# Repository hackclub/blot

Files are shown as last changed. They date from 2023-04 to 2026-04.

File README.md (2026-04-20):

# Blot, the plotter bot from Hack Club

**[🕸 Landing Page](https://blot.hackclub.com)** | **[💻 Online Editor](https://blot.hackclub.com/editor)** | **[👀 Gallery](https://blot.hackclub.com/gallery)**

> Saw Blot at [RMRRF](https://rmrrf.com) 2026? That was a fork of the firmware, check it out [here](https://github.com/samdev-7/upgraded-blot).

Create programmatic art in our web-based editor and submit it to the gallery and we'll send you a CNC machine which can make that art for free.
Blot is a [**You Ship, We Ship**](https://github.com/hackclub/blot/tree/main?tab=readme-ov-file#you-ship-we-ship) project from [Hack Club](https://hackclub.com).

> Everything about Blot is open source. The online editor and drawing library can be freely used by anyone, and we encourage all to submit to the gallery through PRs! However, you must be a teenager or younger to receive a free machine.

blot-white-bg

A piece of art made for Blot can be the first program you ever write, but it can also be a challenge for a master programmer. Check out some of the art made already in our [gallery](https://blot.hackclub.com/gallery). Every piece of art you see is actually a program. Many of them create unique pieces every time the art is run. You may be looking at an artwork which has never been seen before, even by the creator.

For a short video introduction to Blot [check out our 38 second trailer](https://www.youtube.com/watch?v=d1noJNmfvC0).

<a href="https://www.youtube.com/watch?v=d1noJNmfvC0">
  
</a>

# How It Works

### 1) Create a piece of programmatic art in the web editor.

To learn the Blot drawing library follow our [getting started guide](https://blot.hackclub.com/editor?guide=start). Check out the examples in the [gallery](https://blot.hackclub.com/gallery) and then follow along with some of our [guides](https://blot.hackclub.com/guides).

editor

### 2) Submit that art to the public gallery.

The [submission rules to get a Blot for a PR are here](https://github.com/hackclub/blot/blob/main/docs/GET_A_BLOT.md). **You must be a teenager (or younger to qualify for a free machine)** but anyone can make art and make a PR.

[](https://blot.hackclub.com/gallery)

### 3) Receive the parts to build your own Blot that can draw that art in real life.

The [bill of materials can be found here](/docs/BOM.toml) and an [assembly guide here](https://blot.hackclub.com/assembly).

all-parts



<!-- <img height="341" alt="drawing" src="https://github.com/hackclub/blot/assets/27078897/2f7c9c17-3b67-4674-b2ca-2a4dbd26a3d1" /> -->

# Blot is...

**A custom CNC drawing machine** designed from scratch to introduce you to digital fabrication.
It's made of 6 unique 3D printed parts with a custom control board and easy to understand firmware, which can be interfaced with through JavaScript in the browser.
Blot is designed in OnShape. Check out the [3D model of the project](https://cad.onshape.com/documents/536478c2ac00624edd8e2182/w/945ceabd15096661108b7650/e/61fd4346c9fdab983c6ba24d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).
You can find the [bill of materials here](https://blot.hackclub.com/assembly) and, if you'd like to 3D print your Blot, [the parts are here](https://github.com/hackclub/blot/tree/main/hardware/mechanical/drawing-thing-v4). The entire build costs about $150 dollars. If you're a teen we will give you all the parts for a PR with your an art piece you coded yourself.

**A web based editor for programmatic art** that we designed specifically for pen plotting with a [custom geometry library](/docs/DOCUMENTATION.md).
We practiced programmatic pen plotting with [some](https://github.com/LingDong-) [amazing artists](https://static1.squarespace.com/static/63fbc39db5b01b5fa30423db/t/649b424d33b2ce3e0d5b63a5/1687896656015/June+Cohort+Zine.pdf).
There is so much to learn and explore on the programming and the aesthetic side.

parts



# Blot Docs

Here are a collection of resources for Blot:

- [Complete documentation of the drawing library in the editor](https://github.com/hackclub/blot/blob/main/docs/DOCUMENTATION.md)
- [Short documentation shown in the Blot editor](https://github.com/hackclub/blot/blob/main/public/TOOLKIT.md)
- [The Blot assembly and operation guide](https://github.com/hackclub/blot/blob/main/docs/assembly/ASSEMBLY.md)
- [The source of truth bill of materials (BOM)](https://github.com/hackclub/blot/blob/main/docs/BOM.toml)
- [Criteria for how to get a Blot and a guide on how to submit a PR](https://github.com/hackclub/blot/blob/main/docs/GET_A_BLOT.md)
- [A guide on how to review Blot submissions](https://github.com/hackclub/blot/blob/main/docs/BLOT_REVIEW.md)
- [A brief guide on how to approve Blot requests for Blot shipments](https://github.com/hackclub/blot/blob/main/docs/APPROVING_BLOT_REQUESTS.md)
- [Information on how we order Blot supplies from our manufacturing partners](https://github.com/hackclub/blot/blob/main/docs/ORDERING_BLOT_KITS.md)
- [The files for the 3D printed parts](https://github.com/hackclub/blot/tree/main/hardware/mechanical/blot-v6)
- [The source files for the control PCB](https://github.com/hackclub/blot/tree/main/hardware/motor-control-board/circuit/controller)
- [The source files for the power delivery PCB](https://github.com/hackclub/blot/tree/main/hardware/motor-control-board/circuit/power-delivery)
- [The firmware for the Blot control board](https://github.com/hackclub/blot/blob/main/hardware/motor-control-board/firmware/firmware.ino)
- [Sample Blot based lesson plan](https://github.com/hackclub/blot/blob/main/docs/lesson/LESSON-PLAN.md)
- [Video of a Blot being assembled](https://www.youtube.com/watch?v=7N-Nu6_oo4I)
- [Video of operating a Blot](https://www.youtube.com/watch?v=qDP5CNjFHJE)
- [Video of making a Blot submission](https://www.youtube.com/watch?v=AmbjNEPuv14)
- [Video Blot promo trailer](https://www.youtube.com/watch?v=d1noJNmfvC0)
- [Video introduction to JavaScript in the context of Blot](https://www.youtube.com/watch?v=3KAan1PzmxA)
- [Video introduction to Blot editor](https://www.youtube.com/watch?v=OZ9KaFr1V_o)
- [Video demonstrating working through a Blot guide](https://www.youtube.com/watch?v=mP4rUdaF8ng)

# What are People Making with Blot

Blot has been in development since January 2023 and was released April 2024. We've had lots of people use the Blot editor and the Blot machine to create visual art, run workshops and as part of interactive installations. Here's a sense of what can be done with Blot.

### Programmatic Art

There are all sorts of styles of programmatic art. Here are some examples of great Blot submissions that show a range of styles. This list is by no means exhaustive.

**The natural scene** is a common source of artistic inspiration. This could be called figurative or representational art when it tries to depict a real thing with some fidelity. One example are these roots by Kai (age 17).

<a href="https://blot.hackclub.com/editor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">
  collection
</a>

**The geometric pattern** is natural avenue to pursue when making art with computers because code is a great way to describe patterns. Oz's approach of clipping overlapping segments creates a wonderful sense of depth.

<a href="https://blot.hackclub.com/editor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">
  
</a>

**The tech demo (with composition)** is focusing on a specific technical approach like in Henry's (age 15) ray marcher. The art piece isn't complete though until the artists uses the technique to make a composition.

<a href="https://blot.hackclub.com/editor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">
  <picture>
    <source media="(prefers-color-scheme: dark)" srcset="https://github.com/hackclub/blot/assets/61765149/d65464eb-8cc2-4bf3-be82-0b4cc12070bd">
    <source media="(prefers-color-scheme: light)" srcset="https://github.com/hackclub/blot/assets/27078897/90c01a52-0404-423f-8ae9-763bc591ff9f">
    
  </picture>
</a>

**The data transformation** can be seen in Kieran's (age 15) self portrait. It takes data from an SVG but modifies it programmatically to produce an art piece. This approach could be used to visualize data that may not of been visual to begin with.

<a href="https://blot.hackclub.com/editor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">
  
</a>

**The concept** is important with any artwork and can be mixed with any of the genres above. Ultimately an interesting idea can be what elevates something that is visually pretty simple, one example by Ayush is the Blot's own self portrait.

<a href="https://blot.hackclub.com/editor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">
  <picture>
    <source media="(prefers-color-scheme: dark)" srcset="https://github.com/hackclub/blot/assets/61765149/12044cdf-a498-438c-814b-48622488e42f">
    <source media="(prefers-color-scheme: light)" srcset="https://github.com/hackclub/blot/assets/27078897/1f367d9b-aa74-4fca-8623-259a06800335">
    
  </picture>
</a>

For way more examples check out the [gallery](https://blot.hackclub.com/gallery).

### Blot as Creative Material

You ship we ship projects are developed to provide technological creative material. The Blot was developed to not just create visual programs on computers but also to explore robotic and interactive technology. Here are some ways the machine or project has been used to create interactive technology experiences.

[**Lineflow**](https://github.com/leomcelroy/lineflow) was developed as an interactive art piece for an MIT Museum event. Participants would create a single line drawing on the computer and would then watch a simulation of a line folding into their drawing. Three frames of that simulation were strung together to create a timeline of the animation that would be drawn by a Blot to be brought home by the participant.





**The infinite gallery** at [Outernet](https://www.youtube.com/watch?v=O1s5HqSqKi0) (Hack Club's 2023 summer hackathon). Leo, Kai, and Henry constructed a black out box that contained an infinite art gallery. Participant's entered a room sized black box with one wall illuminated with artwork and a giant joystick in the center. They could navigate the gallery with the joystick and as they explored new (possibly never before seen) art was generated based on their location.



**Chinese calligraphy workshop** was developed for and run at the [Hack Club leader summit 2024](https://www.youtube.com/watch?v=UZEm5lONg7g) by Bright Li (age 15). During it participants learned how to draw Chinese calligraphy programmatically and then handed ink brushes to Bright's Blot robot to put the drawings to the page.



# It's All Open Source

Every part of Blot is freely available for you to investigate and discover.
That includes the editor, the hardware design, the electronics, and even the finances around the project.
We think people deserve tools they can take ownership of. That's why we give away the source for free.

Our projects at Hack Club have hundreds of teenage contributors from all over the world. If you want to learn how to program, we invite you to jump in and start building tools used by thousands.

You're also welcome to participate and use our tools if you aren't a teen (like making art or building your own blot), but our [online community](https://hackclub.com/slack) is for teens only.

# You Ship, We Ship

At Hack Club we're reimagining a new type of public education for technology. We believe people learn best by creating things they care about and sharing them with others. We build open source creative tools with young people all around the world. These tools are gateways to new subjects in technology like [embedded systems](https://sprig.hackclub.com), [circuits](https://onboard.hackclub.com) or digital fabrication robotics. When teenagers build things with our tools we send them more creative materials for free.

Our goal is to build a new type of library online that offers learners not just media to consume but tools to create. And it is free and open source to all. We're just getting started...

# Development

Join the `#blot` channel on the [Hack Club Slack](https://hackclub.com/slack).

The Blot editor is run with an Express server.

After installing `Git`, `Node.js`, and `Yarn`, clone the repo.

```
git clone https://github.com/hackclub/blot/
yarn install
```

To run the development server:

```
yarn dev
```

# License

The Hack Club Blot is open source and licensed under the [MIT License](https://github.com/hackclub/blot/LICENSE.md). Fork, remix, and make it your own! Pull requests and other contributions greatly appreciated.

# Acknowledgements

Many people have contributed to Blot, to mention a few and give much thanks too...

MIT's Center for Bits and Atoms for providing expert advice and occasionally a space to work.

Sam Hu and his team at ISourceAsia for supplying Blot parts and becoming a critical part of the Blot team.

Paul Hamilton for his contributions to embedded circuit designs.

Oz Nova for writing an excellent getting started guide.

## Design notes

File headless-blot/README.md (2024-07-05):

# TeleBlot

Blot is a plotter bot from Hack Club. The TeleBlot Site encourages Hack Clubbers to create with Blot by lowering the barrier for Hack Clubbers to see their Blot works drawn on a Blot machine. Hack Clubbers can upload code to the website and watch through a livestream as a remote blot machine (the TeleBlot) draws their code.

image (2)

image (1)

## Components
- Raspberry Pi Model B (RPi)
- LCD Writing Tablet (modified)
- USB Webcam (generic)
- Blot from Hack Club

## Setup
The setup requires:
- [ ] RPi connected to WiFi
- [ ] *USB Webcam* and *Blot* connected to RPi through USB
- [ ] *LCD Writing Tablet* connected to RPi through GPIO (connect the tablet's ground wire to the RPi's ground GPIO pin and the tablet's postive wire to the RPi's BOARD_PIN GPIO, default: 7)
- [ ] Position the *USB Webcam* to look at the *LCD Writing Tablet*

On the RPi in the `headless-blot` directory run:
1. `yarn install`
2. `sudo apt-get install motion`
3. `sudo chown motion:motion /etc/motion`
4. `sudo cp motion.conf /etc/motion/motion.conf`

## Running
1. Start the Motion daemon: `sudo systemctl start motion`
2. Start the server: `yarn run`
3. To test, upload a blot code file (.js) to the "Teleblot" Slack Bot on the Hack Club Slack, you should receive 1) a video of the Blot drawing your sketch and 2) an image of the result.

### Note
- Any changes to motion.conf must be copied to: `sudo cp motion.conf /etc/motion/motion.conf` and the Motion daemon restarted: `sudo systemctl start motion`
- Once started, the Motion daemon will run automatically in the background, even after restarting the RPi
- The USB webcam livestream can be found at http://<rpi_ip>:8081 and exposed externally with a reverse proxy such as [LocalXpose](https://localxpose.io/)

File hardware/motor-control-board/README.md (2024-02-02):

# Blot Control Board

The assembled blot control board is a main board with a set of smaller boards attached to it's headers:

- 1x Blot Control Board ([designed in house](./circuit/controller/))
    - 2x A4988 stepper motor drivers
    - 1x Seeeduino XIAO RP2040
    - 1x USB-C Power Delivery board ([designed in house](./circuit/power-delivery/))
    - 1x Stepper motor breakout board ([designed in house](./circuit/stepper-motor-headers/))

A set of three assembled control boards and decoy boards

The KiCAD project files are provided in the repo and are designed with KiCAD v7. This may not be compatible with previous versions, but you can get the latest version [here](https://www.kicad.org/download/). 

## Carrier Board

The carrier board wires the breakouts together, provides external power circuitry for the A4988 and steppers, and a convenient way to mount the board to the blot machine. It's a simple 2-layer 1.6mm PCB measured at 50x70mm. It also has a pin header breaking out 5 unused GPIO pins, including 1 DAC channel, 2 analog-capable pins, and one I2C bus. 

KiCAD Render of Carrier Board

## Power Delivery Board

The power delivery board provides a fixed output of 9V1A using the CYPD3177 chipset. It's highly flexible, allowing USB-C Charging up to 15W and USB-C PD up to 100W. Unlike many other chips available, it does not require any firmware nor flashing, and power settings are configured with pullup and pulldown resistors. This board is set to 9V @ 1A, to ensure maximum compatibility with most PD-capable bricks. It's very compact, measuring less than 22x32mm with breadboard-friendly mounting, an affordable 2-layer design, and single side SMD component placement. 

During prototyping, we used an off-the-shelf module from Amazon. These only had four 2.54mm pins on the edge of the board and were hard to mount onto the board securely. Building our own also gave us better control over supply of these boards. 

*As a precaution: while this board is breadboard friendly, typical solderless breadboards are only rated up to _5V @ 1A_. Do _not_ use this on a solderless breadboard.*

KiCAD Render of PD Board

## Additional Relevant Reading

Below is a list of datasheets / product briefs that may be relevant. 

[Seeeduino RP2040 XIAO](https://wiki.seeedstudio.com/XIAO-RP2040/)\
[A4988 Breakout Board](https://www.pololu.com/product/1182)\
[CYPD3177](https://www.infineon.com/cms/en/product/universal-serial-bus/usb-c-charging-port-controllers/ez-pd-barrel-connector-replacement-bcr/cypd3177-24lqxq/)\
[DMP3013SFV](https://www.diodes.com/assets/Datasheets/DMP3013SFV.pdf)\
[MM3Z15VC](https://www.onsemi.com/pdf/datasheet/mm3z9v1c-d.pdf)\
[WCAP-ATG5](https://www.we-online.com/components/products/datasheet/860020573008.pdf)\
[JS Series Switch](https://www.ckswitches.com/media/1422/js.pdf)\
[Schottky Diode](https://datasheets.kyocera-avx.com/schottky.pdf)

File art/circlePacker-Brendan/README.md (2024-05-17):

Circle Packer fills the page with circles suboptimally.

Most of the code was reused and adapted from a [project I did a year ago](https://github.com/Brelee2222/CLUCK/blob/main/src/frontend/dash/circlePacker.ts)

The packer works by attempting to fit circles in between two others. If the circle cannot be fit, the size is reduced is attempts to fit the circle again.

These are the following configurable values that will change how the blot will print:<br />
* targetAreaFill -- This value changes how much the circles need to fill of the area before the program stops generating circles.
* minCircleSize -- This value sets a minimum radius a circle needs to be in order to be shown/printed by the blot.
* bt.setRandSeed(seed); -- Sets a seed to the randomness.

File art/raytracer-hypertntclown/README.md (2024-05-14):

# Raytracer

This is a raytracer, currently able to render spheres and triangles, I built based on concepts learned from [Computer Graphics from Scratch](https://gabrielgambetta.com/computer-graphics-from-scratch/). I highly recommend anyone who's interested in building their own raytracer to check this out.

It has two "modes". Mainly there is the one adapted to use a post processing filter to render it as grayscale ascii-art with a limited character-set as otherwise it would for sure not have been able to be drawn by a Blot.
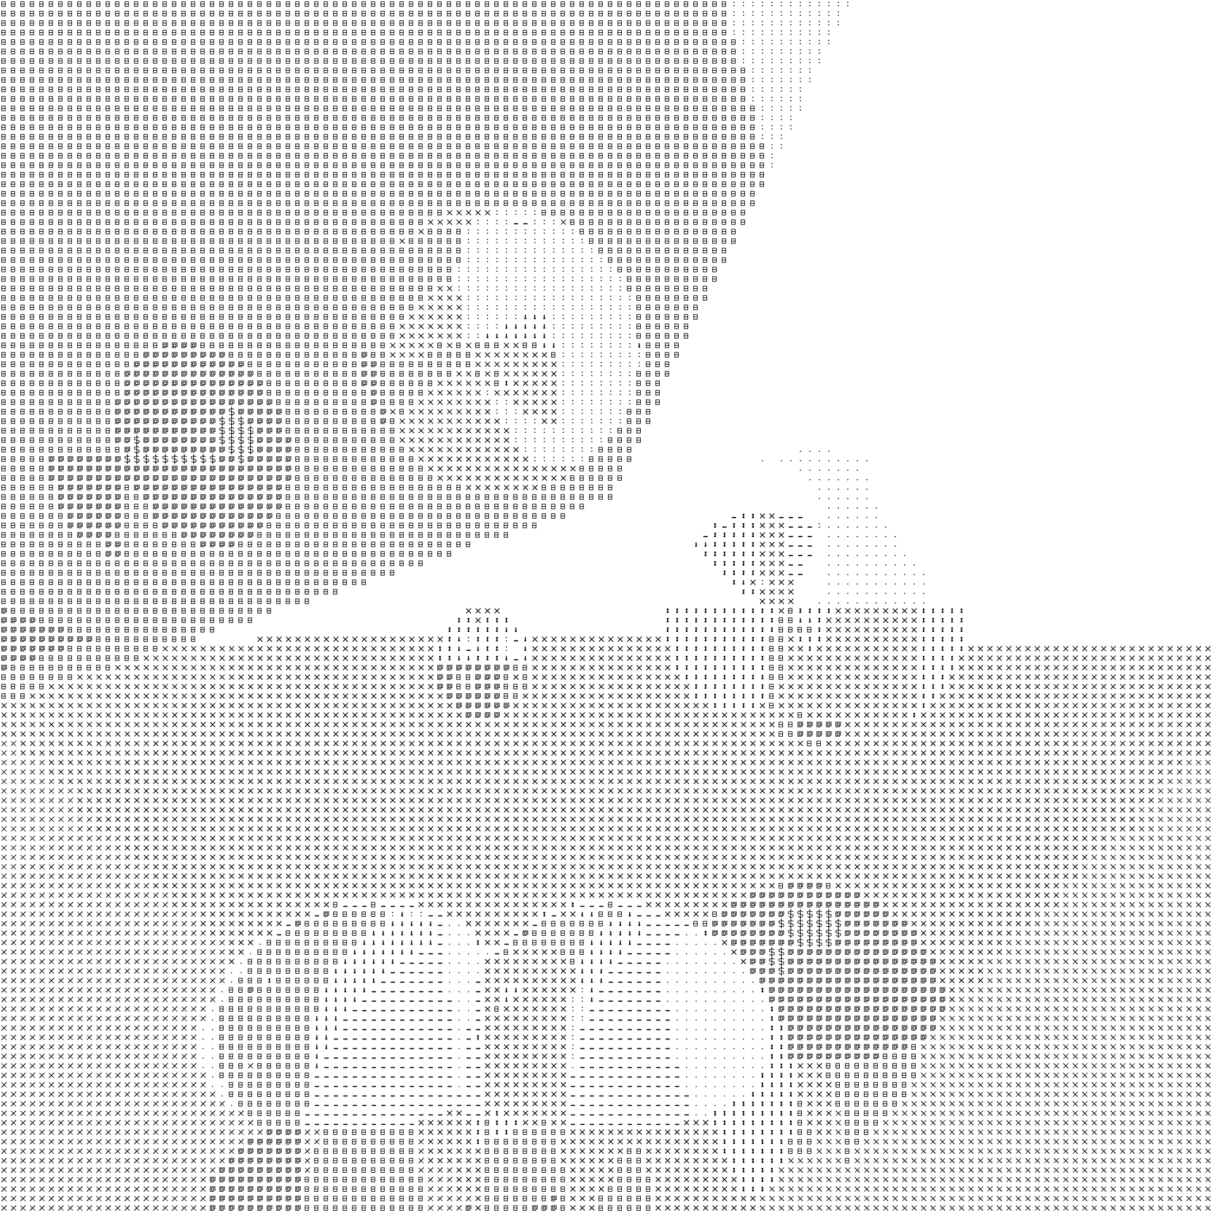
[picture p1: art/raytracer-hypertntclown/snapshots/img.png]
SinArt


The second "mode", activated by changing a boolean at the top of the script, shows the raytraced result before being filtered.
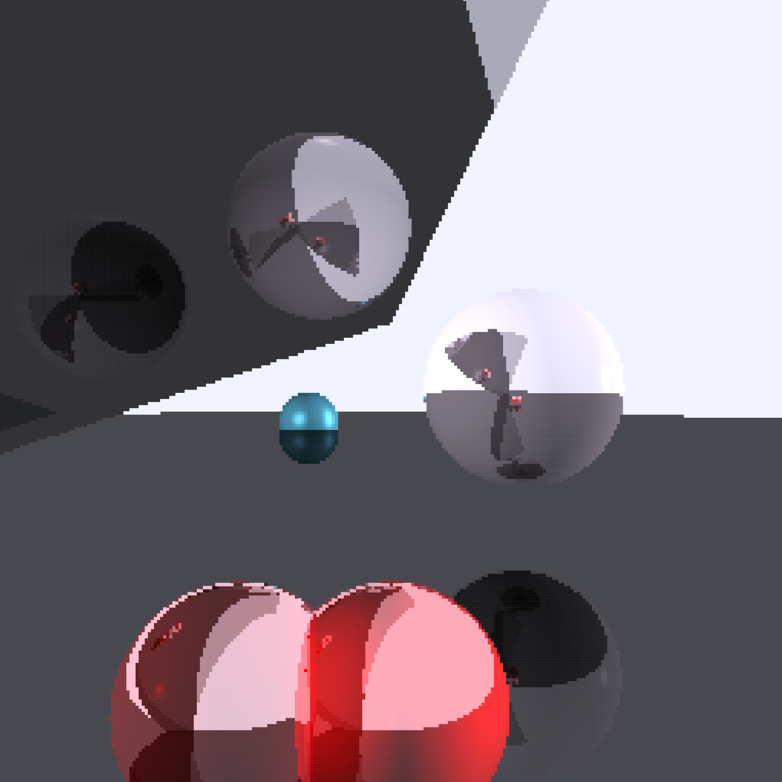
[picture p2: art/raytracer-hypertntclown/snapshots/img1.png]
Raytrace


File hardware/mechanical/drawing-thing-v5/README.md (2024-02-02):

- CarriagePlate.stl is assembled from aluminum plate
- For the carriage, you can either print EccentricCarriage.stl by itself, or print ReinforcedCarriage.stl and add the aluminum CarriagePlate.stl to it during assembly

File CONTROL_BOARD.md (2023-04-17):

# WIP

# [A single control board](https://leomcelroy.com/svg-pcb/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)

Ultimately the idea is that each device will have it's own little board which we network together through modular things. 
For development purposes (and for the sake of doing due diligence) I decided to make a single control board as well which the two steppers and single servo and plug into.
It saves money because the board only requires one xiao instead of three.

I decided to use SVG PCB to design the board because I'm pretty comfortable with the software (because I wrote it).
Additionally, a community contributor to the project (Kris) recently added Gerber export which I was eager to use.

https://tracespace.io/view/
https://www.amazon.com/gp/product/B08NFKV2LD/ref=ppx_yo_dt_b_asin_title_o00_s00?ie=UTF8&psc=1
https://jsoneditoronline.org/#left=local.linisi
https://www.snapeda.com/parts/102010388/Seeed%20Technology%20Co.%2C%20Ltd/view-part/?ref=search&t=xiao

Seeeduino-XIAO-pinout-1
0J10073 600



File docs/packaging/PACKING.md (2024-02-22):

Hey there! If you're reading this, you're probably trying to pack a blot to ship out to a hack clubber.

You'll probably want to familiarize yourself with the [BOM](../BOM.toml) before packing.

Here's a quick checklist of what to include:

- [ ] Welcome to blot letter
- [ ] Box 1: screws
- [ ] Box 2: belt and flanged bearings
- [ ] Box 3: v-wheel box
- [ ] Box 4: nuts
- [ ] Box 5: electronics
- [ ] Tool bundle
- [ ] Floating parts

Each box should be pre-assembled before packing a blot box & each of the parts should be QA tested before going into their respective boxes. Each box has a checklist of parts, and a following section on how to test the parts. Not all parts need to be tested.

## Welcome to blot letter

This is a letter that accompanies every blot. It's a quick, friendly message and includes a screw size guide. It's drawn on small cardstock using a blot.



The code for drawing this on a blot can be found in [notecard.js](./notecard.js). Please make sure to increment the blot number on the card before shipping & documenting on Airtable's list of Blot orders when you send a Blot with a specific number.

## Box 1: screws

- [ ] A paper bag containing:
  - [ ] M3x10 screws (x9) (1 more than required)
  - [ ] metal shims (x6) (1 more than required)
- [ ] M5x20, cyl. head (x1)
- [ ] M5x20 (x6) (1 more than required)
- [ ] M5x35 (x11) (1 more than required)
- [ ] M5x10 (x14) (1 more than required)

**Testing**

A screw size guide is included in the welcome to blot letter. Each group of screws should be tested before being packed.

## Box 2: belt and flanged bearings

- [ ] timing belt
- [ ] 1 flanged bearing tube (which contains at least 10 flanged bearings)

**Testing**

To test the timing belt, hold it up to the master belt and ensure it's at least as long and no longer than 1 inch longer than the master belt.

To test the flanged bearings inside the tube, make sure they take up most of the tube to ensure we don't pack a tube with too few bearings.

## Box 3: v-wheel box

This box should contain:
- [ ] 12 V-wheels (1 more than required).

**Testing**

V-wheels should be tested by inserting a M5 screw of any length to ensure they spin freely.

## Box 4: nuts

This box should contain:
- [ ] M5 T-nut (x14) (1 more than required)
- [ ] M5 nut (x18) (1 more than required)
- [ ] Timing belt pulley (x2)
- [ ] Metal Spacer (x4)
- [ ] Eccentric Spacer (x5)
- [ ] 4 rubber feet stickers

**Testing**

To test the timing belt pulley, quickly screw it into a stepper motor and try turning the motor to ensure it has a firm grip on the stepper motor axle.

## Box 5: Electronics

The electronics box should contain:
- [ ] usb-c power cable + brick
- [ ] usb-c male-male data cable
- [ ] 2 stepper motor 6-pin to 4-pin cables
- [ ] anti-static bag containing:
  - [ ] [blot main board](../../hardware/motor-control-board), assembled & packed in an anti-static bag
    - [ ] 2 stepper driver
    - [ ] 1 xiao seeed rp2040
    - [ ] usb-c power distribution board
    - [ ] [horizontal stepper breakout](https://cloud-9z8rqqzj6-hack-club-bot.vercel.app/0img_0759.jpg)
  - [ ] servo motor
  - [ ] servo motor arm

**Testing**

To test the electonics, plug the steppers and servo into the main board, and try to run any of the art examples in the gallery.[^0][^1]

[^0]: Your xiao rp2040 will flash 3 times on it's red LED if flashed.
[^1]: If your xiao rp2040 isn't flashed, or acting strangly, use the flashing instructions provided in [the hardware instructions](../../hardware/motor-control-board/SETUP.md).

The computer should connect properly to the board.
The steppers should move firmly without clicking, and should resist the user pushing them. To test resistance, you may need to attach the Timing belt pulley from [box 4](#box-4-spacers-and-pulleys-box) to the stepper motor.

## Tool bundle

The taped-together tool bundle should contain:
- [ ] 2mm allen key
- [ ] 2.5mm allen key
- [ ] 5mm allen key
- [ ] 10mm wrench
- [ ] 1 retractable/ballpoint pen

**Testing**

Try to fit each allen key into a screw of a corresponding size. There are many allen keys around the office and we want to make sure we haven't mixed up a slightly different size into the bundle.

## Floating parts

In addition to all the smaller boxes, there are a few parts that go directly into the main package:
- [ ] 2 stepper motors
- [ ] wrapping/stuffing paper for padding(optional)
- [ ] aluminum parts:
  - [ ] carriage plate
  - [ ] 2020x250mm extrusion (x2)
- [ ] The 3d printed components
  - The full list can be found on [the bom](../BOM.toml)

**Testing**

The aluminum parts are a little roughly cut. Run your finger over them for signs of sharp edges/burrs. If you find any, use another or file it down to smooth it out.

The aluminum extrusion should be measured to ensure it's from good stock. We have multiple sizes in the office and we want to make sure we don't pack the wrong size. The bar should be roughly 1ft long.

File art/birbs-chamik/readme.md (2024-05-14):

## birbs

Birbs is an implementation of the artificial life program [Boids](https://en.wikipedia.org/wiki/Boids). Based just on few simple rules it's able to simulate flocking of birds.

There are a lot of variables along with their descriptions at the top of the script that radically change the result of each execution. Enjoy!

### Gallery

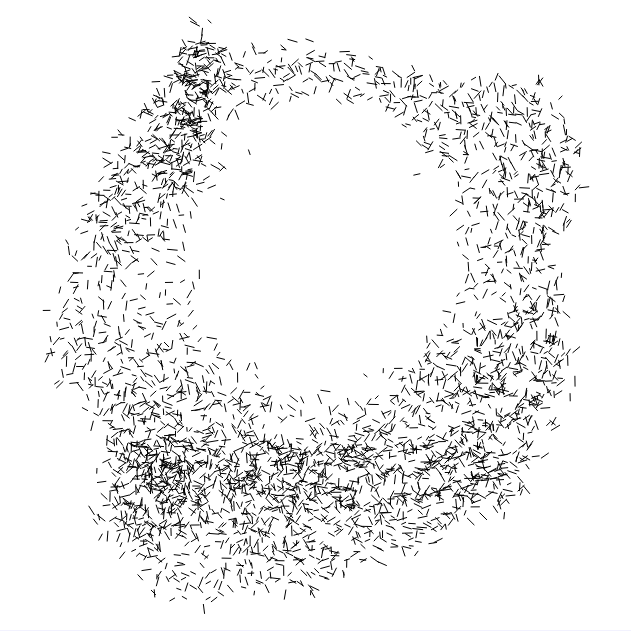
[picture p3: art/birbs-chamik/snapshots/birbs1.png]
birbs 1

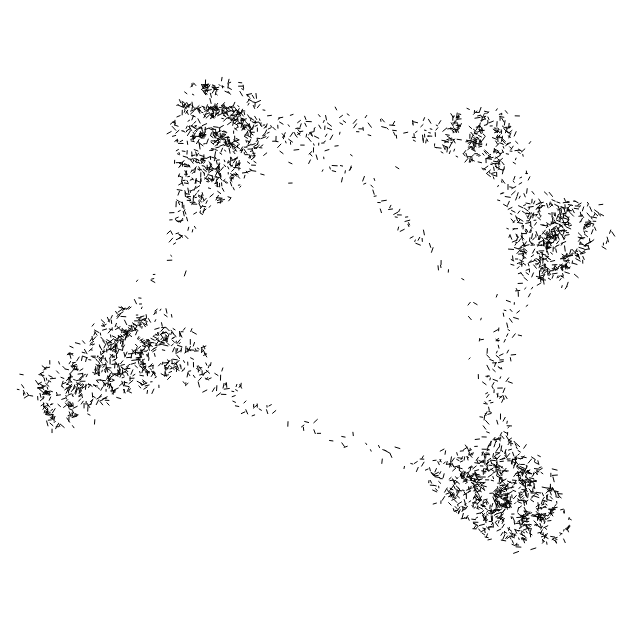
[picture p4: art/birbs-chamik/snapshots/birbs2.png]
birbs 2

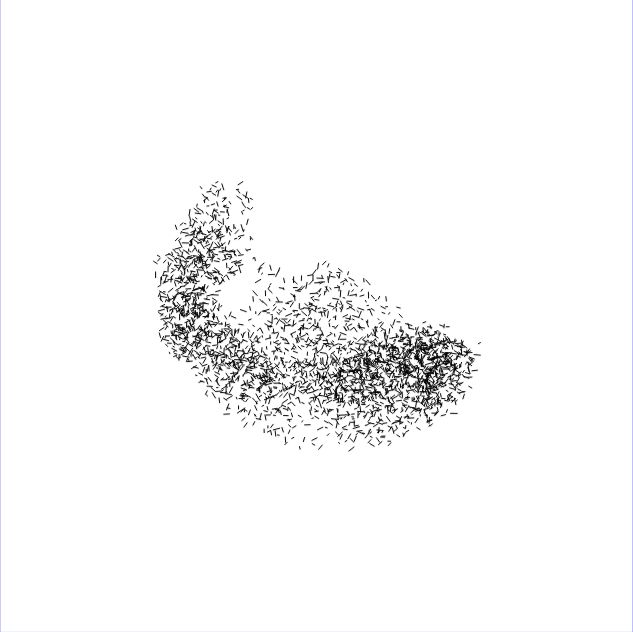
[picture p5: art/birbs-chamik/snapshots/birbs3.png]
birbs 3

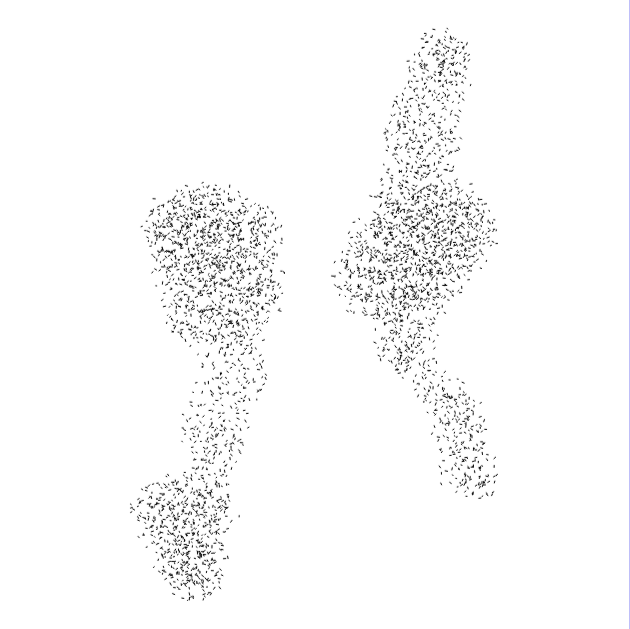
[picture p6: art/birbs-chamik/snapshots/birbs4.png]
birbs 4


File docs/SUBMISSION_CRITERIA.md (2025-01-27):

# Submission Criteria

## What to include:

*While there are no specific criteria we look for, we generally want a strong mix of the following:*

### Visual Engagement
Aleks' Fragmented Horizon is a great example of a detailed, intentionally drawn scene made with Blot. Pieces such as these are great examples of creative intent
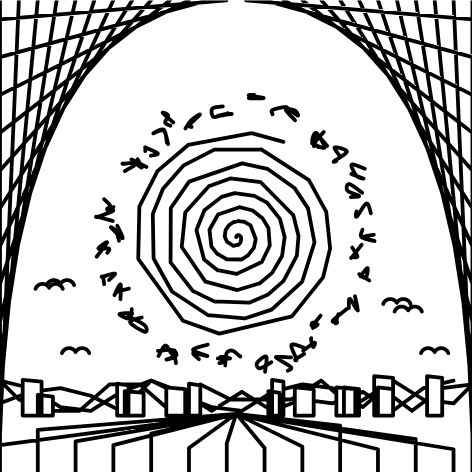
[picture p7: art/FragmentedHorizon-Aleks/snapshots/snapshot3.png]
Fragmented Horizon


### Technical Complexity
Art pieces that push the technical limits of Blot are usually interesting, engaging projects, and so we generally encourage you to do so if you are considering it! For example, Patricio's wireframe renderer can take any set of 3D coordinates and draw it on Blot. Isn't that amazing?
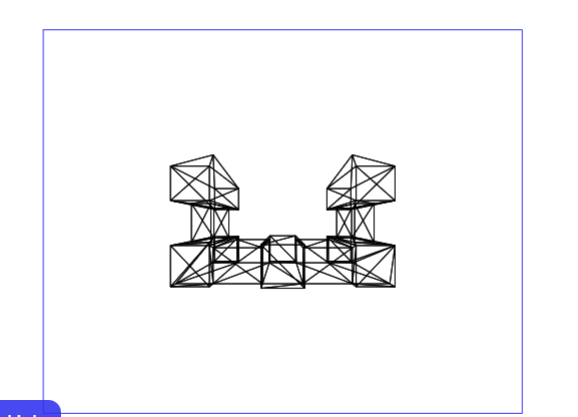
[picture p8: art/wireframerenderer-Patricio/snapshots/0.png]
Wireframe Renderer


### Polish & Aesthetics
The art piece should be aesthetically pleasing & feel like a polished piece of work. For example, this mushroom piece by Xinyang, though it may appear simple at first, is well-put together appears polished
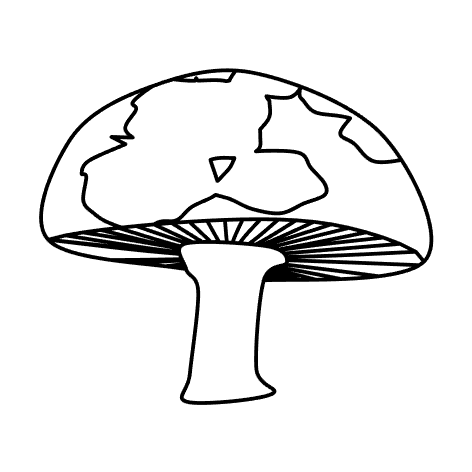
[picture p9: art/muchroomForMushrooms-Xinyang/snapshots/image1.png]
MushroomScreenshot


Your submission should be a combination of the above in varying degrees.

## What not to include:

### Linearly generated patterns


These patterns generally do not require much creative thought and are easy to generate!

### Stolen art with a few variables changed
Make your own art!

## Some final notes

- **Your artwork must be generative.** You should have some variables at the top that are controlled by randomness functions such as `bt.randIntInRange()` that change the artwork

- **Your artwork should be drawable by Blot**, which means it shouldn't excessively cross a certain area multiple times. The general guideline is that crossing over one point any more than 5 times will rip the paper.

- **Your artwork should not rely on the fill option.** (This includes color or filling with black) Unfortunately, Blot doesn't understand the fill option yet. Maybe you can be the first to add it! In the mean time, you can use thin stripes to effectively shade an area.

## Submitting
If you feel like your art piece meets these requirements, you can find the submission instructions **[here.](https://github.com/hackclub/blot/blob/main/docs/GET_A_BLOT.md)** 
Most artwork takes around 15-20 hours of work to get accepted, so make sure you really polish it before submitting.

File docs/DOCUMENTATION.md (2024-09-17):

# The Toolkit  

This is the drawing library available in the Blot editor.

---

## Environment Affecting

These functions set properties of the Blot drawing environment.

### setDocDimensions(width, height)

**Parameters:**
- `width` (number): The width of the document.
- `height` (number): The height of the document.

**Returns:** Nothing.

**Description:** 

Sets the dimensions of the drawing document.
This function initializes the size of the drawing area, it's used as a visual cue.
The workarea of the Blot is 125mm by 125mm. 
It is usually one of the first functions called when setting up a new drawing. 
The bottom left corner is 0,0. 
The units are millimeters (mm).

**Example:**
```js
setDocDimensions(800, 600);
```

### drawLines(polylines)

**Parameters:**
- `polylines` ([number, number][][]): A list of polylines

**Returns:** Nothing.

**Description:**

Draws a copy of the polylines passed onto the screen. 

**Example:**

```js
drawLines([
  [
    [0, 0],
    [100, 100]
  ]
]);
```

## Importing the blotToolkit

The functions below are available in the `blotToolkit` object.

```js
// like so
blotToolkit.scale(...)
```

`blotToolkit` is also available as the abbreviated `bt`. This is **the recommended way to reference the blotToolkit**.

```js
// like so
bt.scale(...)
```

You can also destructure the functions from `blotToolkit`.

```js
// all imports
const { Turtle, trim, merge, cut, cover, rotate, scale, translate, originate, iteratePoints, pointInside, resample, join, copy, union, difference, intersection, xor, getAngle, getPoint, getNormal, bounds, nurbs, catmullRom, rand, setRandSeed, randInRange, randIntInRange, noise } = blotToolkit;
```

```js
// common imports
const { Turtle, cut, cover, copy, rotate, scale, translate, originate, iteratePoints, resample, join, getAngle, getNormal, bounds, rand, setRandSeed, randInRange, noise, nurbs } = blotToolkit;
```

## Modify Polylines

These functions modify a polyline that is passed as a first argument.

### iteratePoints(polylines, callback)

**Parameters:**
  - `polylines` ([number, number][][]): An array of polylines to iterate over.
  - `callback` (Function): A function that is called for each point with parameters:
    - `pt` ([number, number]): The current point.
    - `t` (number): The normalized position of the point in the polyline.

**Returns:** 
The original array of polylines with the points modified by the callback function. 
Points are mutated in place.

**Description:**

This function iterates over each point in a set of polylines. 
The provided callback function can modify each point by returning a new point, 
split the polyline by returning `"BREAK"`, 
or remove a point by returning `"REMOVE"`. 
The callback receives the current point and its normalized position within the polyline. 
Modifications are applied after all points are iterated through.

**Example:**

```js
const polylines = [[[0, 0], [10, 10], [20, 20]]];
const modifiedPolylines = bt.iteratePoints(polylines, (pt, t) => {
  const [x, y] = pt;
  // Move each point up by 5mm
  return [x, y + 5];
});

// or 

const modifiedPolylines2 = bt.iteratePoints(polylines, (pt, t) => {
  const [x, y] = pt;

  if (t < .2) {
    return "REMOVE";
  } else if (.5 > rand()) {
    return "BREAK";
  }

  // Move each point up by 5mm
  return [x, y + 5];
});
```

### scale(polylines, scale, origin = [0, 0])

**Parameters:**
  - `polylines` ([number, number][][]): An array of polylines to be scaled.
  - `scale` (number | [number, number]): The scale factor to apply. If a single number is provided, the scale is uniform across both axes. If an array is provided, it specifies separate scale factors for the x (`scaleX`) and y (`scaleY`) dimensions.
  - `origin` ([number, number], optional): The point around which the scaling is performed. Defaults to bounding box center if not specified.

**Returns:** A new array of polylines that have been scaled according to the specified parameters.

**Description:**

Scales the provided polylines by a specified factor, 
optionally around a custom origin point. 
This can uniformly or non-uniformly transform the size of the polylines.
It supports both uniform scaling (where the shape's proportions are maintained) and non-uniform scaling (where the shape's proportions can change). 
The function allows for scaling around a specific origin point. 
The default origin is the center of the bounding box of the shape.

**Example:**

```js
const polylines = [
  [[0, 0], [10, 0], [10, 10], [0, 10], [0, 0]]
];

// Scale uniformly by a factor of 2
const uniformlyScaled = bt.scale(polylines, 2);

// Scale non-uniformly (x by 2, y by 3)
const nonUniformlyScaled = bt.scale(polylines, [2, 3]);

// Scale uniformly around a custom origin (5, 5)
const customOriginScaled = bt.scale(polylines, 2, [5, 5]);
```

### rotate(polylines, degrees, origin = [0, 0])

**Parameters:**
  - `polylines` ([number, number][][]): An array of polylines to be rotated.
  - `degrees` (number): The angle in degrees by which the polylines should be rotated. Positive values rotate the shape clockwise, while negative values rotate it counterclockwise.
  - `origin` ([number, number], optional): The point around which the rotation will occur. Defaults to bounding box center if not specified.

**Returns:** The modified array of polylines after rotation.

**Description:**

Rotates the provided polylines around a specified origin point by a given number of degrees. 

**Example:**

```js
const polylines = [[[10, 10], [20, 20], [30, 10]]];
const degrees = 45; // Rotate 45 degrees clockwise

bt.rotate(polylines, degrees);
bt.rotate(polylines, degrees, [45, 0]);
```

### translate(polylines, [dx, dy], origin = [0, 0])

**Parameters:**
  - `polylines` ([number, number][][]): An array of polylines to be translated.
  - `[dx, dy]` ([number, number]): The distance to move the polylines along the x (dx) and y (dy) axes.
  - `origin` ([number, number], optional): The point from which the translation is performed. Defaults to `[0, 0]` if not specified.

**Description:**

Translates (moves) the provided polylines by a specified distance along the x and y axes, optionally from a custom origin point. This modification is applied directly to the provided array of polylines.
The `translate` function shifts the position of the given polylines without altering their shape or orientation. It's useful for repositioning drawings within a graphical space or relative to other elements.

**Returns:** The modified array of polylines after translation.

**Example:**

```js
const polylines = [[[0, 0], [10, 10], [20, 5]]];
bt.translate(polylines, [5, 10]);
```

### originate(polylines)

**Parameters:**
  - `polylines` ([number, number][][]): An array of polylines to be centered.

**Returns:** The modified array of polylines after centering at the coordinate origin.

**Description:**

Moves the center of the provided polylines to the coordinate origin ([0, 0]). 
This modification is applied directly to the provided array of polylines.
The `originate` function recalculates the bounding box of the given polylines and translates them such that their center aligns with the origin of the coordinate system. This is particularly useful for standardizing the position of shapes before applying transformations like rotation or scaling.

**Example:**

```js
const polylines = [[[10, 10], [20, 20], [30, 10]]];
bt.originate(polylines);
```

### resample(polylines, sampleRate)

**Parameters:**
  - `polylines` ([number, number][][]): An array of polylines to be resampled.
  - `sampleRate` (number): The new distance between adjacent points on the polyline.

**Returns:** The modified array of polylines after resampling.

**Description:**
Adjusts the density of points along the polylines according to a specified sample rate, effectively changing the resolution of the shape. This modification is applied directly to the provided array of polylines.
The `resample` function is used to either increase or decrease the number of points along a polyline, based on the specified sample rate.

**Example:**

```js
const polylines = [[[0, 0], [10, 10], [20, 5], [30, 10]]];
bt.resample(polylines, 5);
```

### simplify(polylines, tolerance, highQuality = false)

**Parameters:**
  - `polylines` ([number, number][][]): An array of polylines to be simplified.
  - `tolerance` (number): The maximum allowed deviation from the original line.
  - `highQuality` (boolean, optional): If true, uses a slower algorithm that ensures a higher quality of simplification. Defaults to false.

**Returns:** The modified array of polylines after simplification.

**Description:**

Reduces the number of points in a polyline while retaining its general shape, based on a specified tolerance. This modification is applied directly to the provided array of polylines.
The `simplify` function is particularly useful for reducing the complexity of polyline shapes, which can be beneficial for performance optimization in rendering and for creating a more abstract visual appearance.

**Example:**

```js
const polylines = [[[0, 0], [5, 5], [10, 10], [15, 15], [20, 20]]];
bt.simplify(polylines, 1);
```

### trim(polylines, tStart, tEnd)

**Parameters:**
  - `polylines` ([number, number][][]): An array of polylines to be trimmed.
  - `tStart` (number): The start position of the trim, normalized to the range [0, 1].
  - `tEnd` (number): The end position of the trim, normalized to the range [0, 1].

**Returns:** The modified array of polylines after trimming.

**Description:**

Trims the polylines to a specified range, based on normalized positions along their length. This modification is applied directly to the provided array of polylines.
The `trim` function reduces the length of each polyline according to the specified start and end positions. This is useful for cutting away unwanted sections of a polyline or isolating specific portions of interest.

**Example:**

```js
const polylines = [[[0, 0], [10, 10], [20, 20]]];
bt.trim(polylines, 0.25, 0.75);
```

### merge(polylines)

**Parameters:**
  - `polylines` ([number, number][][]): An array of polylines to be merged.

**Returns:** The modified array containing a single polyline after merging.

**Description:**

Merges multiple polylines with overlapping endpoints into a single polyline. This modification is applied directly to the provided array of polylines.
The `merge` function combines several polyline paths into one continuous path, effectively joining them end-to-end. This is useful for creating single, coherent shapes out of multiple segments.

**Example:**

```js
const polyline1 = [[0, 0], [10, 10]];
const polyline2 = [[10, 10], [20, 20]];
const polylines = [polyline1, polyline2];
bt.merge(polylines);
```

### join(polylines0, ...morePolylines)

**Parameters:**
  - `polylines0` ([number, number][][]): The primary array of polylines to which others will be joined.
  - `...morePolylines` ([number, number][][]): Additional arrays of polylines to be joined to the first.

**Returns:** The modified first array of polylines after joining.

**Description:**
Joins multiple arrays of polylines into a single array, concatenating them. 
This modification is applied directly to the first provided array of polylines.
The `join` function is used to concatenate multiple arrays of polylines into a single array, allowing for the combination of separate polyline collections into one.

**Example:**

```js
const polylines1 = [[[0, 0], [10, 10]]];
const polylines2 = [[[20, 20], [30, 30]]];
bt.join(polylines1, polylines2);
```

### copy(polylines)

**Parameters:**
  - `polylines` ([number, number][][]): An array of polylines to be copied.

**Returns:** A new array of polylines that is a deep copy of the provided polylines.

**Description:**

Creates a deep copy of the provided polylines. 
This function does not modify the provided array but returns a new one that is a copy.
The `copy` function is useful when you need to duplicate polylines without altering the original set, allowing for non-destructive transformations or manipulations on the copy.

**Example:**

```js
const originalPolylines = [[[0, 0], [10, 10]]];
const copiedPolylines = bt.copy(originalPolylines);
```

### cut(polylines0, polylines1)

**Parameters:**
  - `polylines0` ([number, number][][]): The primary array of polylines to be cut.
  - `polylines1` ([number, number][][]): The array of polylines used as the cutter.

**Returns:** The modified `polylines0` array after being cut by `polylines1`.

**Description:**

Removes all points of the `basePolylines` outside of the `cuttingPolylines`.

**Example:**

```js
const polylinesToCut = [[[0, 0], [10, 10], [20, 0]]];
const cuttingPolylines = [[[5, 5], [15, 5]]];
bt.cut(polylinesToCut, cuttingPolylines);
```

### cover(polylines0, polylines1)

**Parameters:**
  - `polylines0` ([number, number][][]): The primary array of polylines to be covered.
  - `polylines1` ([number, number][][]): The array of polylines used to cover the first.

**Returns:** The modified `polylines0` array after being covered by `polylines1`.

**Description:**

Removes all points of the `basePolylines` inside of the `coveringPolylines`.

**Example:**

```js
const basePolylines = [[[0, 0], [10, 10], [20, 0]]];
const coveringPolylines = [[[5, -5], [15, 15]]];
bt.cover(basePolylines, coveringPolylines);
```

### union(polylines0, polylines1)

**Parameters:**
  - `polylines0` ([number, number][][]): The first array of polylines.
  - `polylines1` ([number, number][][]): The second array of polylines.

**Returns:** The modified `polylines0` array after union with `polylines1`.

**Description:**

Takes the boolean union of both sets of polylines.

**Example:**

```js
const subjectPolylines = [[[0, 0], [10, 10], [20, 0]]];
const clippingPolylines = [[[10, 10], [30, 10], [20, -10]]];
bt.union(subjectPolylines, clippingPolylines);
```

### difference(polylines0, polylines1)

**Parameters:**
  - `polylines0` ([number, number][][]): The primary array of polylines to be modified.
  - `polylines1` ([number, number][][]): The array of polylines used to subtract from the first.

**Returns:** The modified `polylines0` array after the difference operation with `polylines1`.

**Description:**

Subtracts the `clippingPolylines` from the `subjectPolylines`.

**Example:**

```js
const subjectPolylines = [[[0, 0], [20, 0], [10, 20]]];
const clippingPolylines = [[[0, 10], [20, 10], [10, -10]]];
bt.difference(subjectPolylines, clippingPolylines);
```

### intersection(polylines0, polylines1)

**Parameters:**
  - `polylines0` ([number, number][][]): The first array of polylines.
  - `polylines1` ([number, number][][]): The second array of polylines.

**Returns:** The modified `polylines0` array after finding the intersection with `polylines1`.

**Description:**

Modifies the `subjectPolylines` to only the part that intersects with the `clippingPolylines`.

**Example:**

```js
const subjectPolylines = [[[0, 0], [10, 10], [20, 0]]];
const clippingPolylines = [[[0, 10], [10, 0], [20, 10]]];
bt.intersection(subjectPolylines, clippingPolylines);
```

### xor(polylines0, polylines1)

**Parameters:**
  - `polylines0` ([number, number][][]): The first array of polylines.
  - `polylines1` ([number, number][][]): The second array of polylines.

**Returns:** The modified `polylines0` array after the xor operation with `polylines1`.

**Description:**

Performs an exclusive or operation on two sets of polylines, leaving only the parts of each set that do not overlap with the other. This operation modifies the first set of polylines directly.

**Example:**

```js
const polylines0 = [[[0, 0], [10, 10], [20, 0]]];
const polylines1 = [[[0, 10], [10, 0], [20, 10]]];
bt.xor(polylines0, polylines1);
```

### offset(polylines, delta, ops = { endType, joinType, miterLimit, arcTolerance })

**Parameters:**
- `polylines` ([number, number][][]): The array of polylines.
- `delta` (number): Distance between offset polylines and target polylines.
- `ops` (object, optional): Configuration options for the offset curve.
  - `endType` ("openSquare" | "openRound" | "openButt" | "closedLine" | "closedPolygon"): End type of the offset. Defaults to "closedPolygon" if closed and "openRound" if open.
  - `joinType` ("square" | "round" | "miter"): Join type of the offset. Defaults to "round".
  - `miterLimit` (number): Miter limit. Defaults to 2.
  - `arcTolerance` (number): Rounding precision. Defaults to 0.1.

**Returns:** A polyline ([number, number][]) of the given shape offset along its normal.

**Description:** 

Can be used to expand, contract, or thicken curves. If passed an open curve it will thicken it with a closed curve around it. If passed a closed curve it will contract or expand based on the sign of delta.

**Example:**

```js
// thicken an open curve
const polylines0 = [[[0, 0], [10, 10], [20, 0]]];
bt.offset(polylines0, 3);

// expand a closed curve
const polylines1 = [[[0, 0], [10, 10], [20, 0], [0, 0]]];
bt.offset(polylines1, 3);

// thicken a closed curve
const polylines2 = [[[0, 0], [10, 10], [20, 0], [0, 0]]];
bt.offset(polylines2, 3, { endType: "openRound" });
```
## Get Data From Polylines

These functions take polylines and return other values. 
They do not modify the polylines.

### getAngle(polylines, t: [0 to 1])

**Parameters:**
- `polylines` ([number, number][][]): An array of polylines representing a shape.
- `t` (number): Normalized position along the polylines where the angle is calculated. Should be between 0 and 1.

**Returns:** The angle in degrees at the specified point along the polylines.

**Description:** 

Calculates the angle in degrees at the specified point along the polylines. 
This function determines the angle of the tangent line to the shape at the given position `t`.

### getPoint(polylines, t: [0 to 1])

**Parameters:**
- `polylines` ([number, number][][]): An array of polylines representing a shape.
- `t` (number): Normalized position along the polylines where the point is obtained. Should be between 0 and 1.

**Returns:** The point coordinates `[x, y]` at the specified position along the polylines.

**Description:** 

Returns the coordinates of the point at the specified position `t` along the polylines. 

### getNormal(polylines, t: [0 to 1])

**Parameters:**
- `polylines` ([number, number][][]): An array of polylines representing a shape.
- `t` (number): Normalized position along the polylines where the normal vector is obtained. Should be between 0 and 1.

**Returns:** The normal vector `[x, y]` at the specified position along the polylines.

**Description:** 

Calculates the normal vector at the specified point along the polylines. 
The normal vector is a vector that is perpendicular to the tangent line at the given position `t`. 

### pointInside(polylines, pt)

**Parameters:**
- `polylines` ([number, number][][]): An array of polylines representing a shape.
- `pt` ([number, number]): The point `[x, y]` to test for containment within the shape.

**Returns:** 
- `true` if the point is inside the shape.
- `false` if the point is outside the shape.

**Description:** 

Determines whether a point lies inside the provided shape defined by the polylines. 
This function is useful for collision detection, hit testing, or determining containment of points within shapes.

### bounds(polylines)

**Parameters:**
- `polylines` ([number, number][][]): An array of polylines representing a shape.

**Returns:** 
An object containing bounding box information:
- `xMin`, `xMax`: The minimum and maximum x-coordinates of the bounding box.
- `yMin`, `yMax`: The minimum and maximum y-coordinates of the bounding box.
- `lt`, `ct`, `rt`, `lc`, `cc`, `rc`, `lb`, `cb`, `rb`: Coordinates of the bounding box corners (left-top, center-top, right-top, left-center, center-center, right-center, left-bottom, center-bottom, right-bottom).
- `width`, `height`: Width and height of the bounding box.

**Description:** 

Calculates the bounding box of the provided shape defined by the polylines. 

They are arranged in this configuration around the bounding box of the polylines

```
lt--ct--rt
 |   |   |
lc--cc--rc
 |   |   | 
lb--cb--rb
```

**Example:**

```js
const polylines = [[[0, 0], [10, 10], [20, 0]]];
const boundingBox = bt.bounds(polylines);
/*
returns { 
  xMin, xMax, 
  yMin, yMax, 
  lt, ct, rt, 
  lc, cc, rc,
  lb, cb, rb,
  width, height
}
*/

const center = boundingBox.cc;
```

## Generate Polylines

A collection of functions and classes for creating polylines.

### Turtle

A `Turtle` class represents a cursor that moves around a canvas to draw shapes. It is inspired by the Logo programming language and can be used to create intricate designs and patterns programmatically.

**Methods:**

- `forward(distance)` Moves the turtle forward by the specified distance, drawing a line if the pen is down.
- `arc(angle, radius)` Draws an arc with the specified angle and radius from the current position.
- `goTo([x, y])` Moves the turtle to the specified coordinates, drawing a line if the pen is down.
- `jump([x, y])` Moves the turtle to the specified coordinates without drawing a line.
- `step([dx, dy])` Moves the turtle to the current positon plus the passed delta values.
- `right(angle)` Rotates the turtle to the right by the specified angle.
- `left(angle)` Rotates the turtle to the left by the specified angle.
- `setAngle(angle)` Sets the absolute angle of the turtle's orientation.
- `up()` Lifts the pen so that moving the turtle does not draw lines.
- `down()` Lowers the pen so that moving the turtle draws lines.
- `copy()` Creates a copy of the turtle's current state.
- `applyToPath(fn)` Takes a function that receives the turtle's path as an argument.
- `lines()` Returns a copy of the Turtle's path.

**Properties:**

- `pos` The current position of the turtle as an `[x, y]` array.
- `angle` The current orientation angle of the turtle.
- `path` The path drawn by the turtle, represented as an array of polylines `[number, number][][]`.
- `drawing` A boolean indicating whether the turtle is currently drawing.

**Example:**

```js
const myTurtle = new bt.Turtle()
  .down()
  .forward(100)
  .right(90)
  .forward(100);
const position = myTurtle.pos; // Gets the current position of the turtle
const path = myTurtle.path; // Gets the path drawn by the turtle, use this to get polylines
```

## Text Creation
Blot contains a limited subset of procedurally created characters, including an instruction parser for "compressed" turtle programming.

### text(str, origin, scale = 100, spacing = [2.5,4.5])

**Parameters:**

- `str` (string): A string of characters to draw. Supports A-Z, 0-9, newlines and some other characters.
- `origin` ([number, number]): Origin(bottom-left hand) position to start drawing letters from.
- `scale` (number, optional): Scaling of drawn letters. Defaults to `100` times original size.
- `spacing` ([number, number], optional): Default spacing between individual letters, multiplied with scale. X is correspondant to X-axis spacing, and Y is likewise for Y-axis spacing. Defaults to `[2.5,4.5]`

**Returns:** An array of polylines ([][][number, number]) corresponding to each of the drawn characters.

**Description:** 

Generates an array of polylines from the provided string, with given origin, scaling and spacing.

**Example:**

```js
// Generate the provided string at position 0,0 with scale of 14
bt.text("Hello world!",[0,0],14)
```

### fromInstructions(inst, org?, scale = 1, returnEndpoint = false)

**Parameters:**

- `inst` (string): String containing instructions for the function to interpret and run.
- `org?` ([number, number]): Origin to run the instructions from. If unspecified, defaults to (0,0).
- `scale` (number): Number to scale instructions given by. If unspecified, does not scale.
- `returnEndpoint` (boolean): Return the last point and polylines instead of just the drawn polylines. If unspecified, function returns polylines only.

**Returns:** An array of polylines generated by the instructions parsed and interpreted. If `returnEndpoint` is true, returns both endpoint and polylines.

**Description:**

A function that contains a limited subset of turtle functions for use in procedural programming. Used internally by `bt.text` for drawing text.

Instructions follow the format of `command1$arg1:arg2,command2$arg1`. Instructions should always be in a single string, with no newlines or breaks. Parameters are seperated from commands by `$`, parameters are seperated from eachother by `:` and whole commands are seperated by `,`.

Instruction|Description|Parameters|Notes
---|---|---|---
`u`|Pen up|None|n/a
`d`|Pen down|None|n/a
`f`|Move turtle forward|Length(mm)|Supports negative length for moving in the opposite direction.
`arc`|Draw an arc|Angle(º), Radius(mm)|n/a
`jmp`|Jumps turtle to the given point.|Point X(mm), Point Y(mm)|n/a
`sa`|Set absolute angle|Angle(Degrees)|0º points the turtle to the top of the screen.
`l`|Turn turtle left|Angle(º)|n/a
`r`|Turn turtle right|Angle(º)|n/a

**Example:**

```js
// Draw the Nixie tube counter as seen on the packaging notecard
setDocDimensions(58,12)

const buildno = 1337
const allLines = []

const CreateTube = (char, org, scale) => {
    let lines = []
    if (typeof bt.letters[char[0]] == "function") {
        lines.push(...bt.letters[char[0]](org, scale))
    } else {
        lines.push(...bt.fromInstructions(bt.letters[char[0]], org, scale))
    }

    lines.push(...bt.fromInstructions("u,sa$90,f$4.5,l$90,d,f$.5,l$90,f$4.5,arc$-90:.5,f$2,arc$-90:.5,f$4.5,l$90,f$.5,arc$90:1,sa$270,u,f$0.025,d,arc$90:1", org, scale))
    lines.push(...bt.fromInstructions("u,sa$270,f$0.5,d,f$1,u,l$90,f$.5,l$90,d,f$1,u,r$90,f$.5,r$90,d,f$1,u,l$90,f$.5,l$90,d,f$1,u,r$90,f$.5,r$90,d,f$1", org, scale))

    return lines
}

allLines.push(...bt.text("Build No. ", [3, 4], 0.82))

const tubeOrg = [51, 3.14]
const tubeScale = 1.35
for (let i = 0; i <= 6; i++) {
    if (i == 0) {
        allLines.push(...CreateTube("#", [tubeOrg[0] + 3.5 * tubeScale * (i - 6), tubeOrg[1]], tubeScale))
        continue
    }
    allLines.push(...CreateTube((Math.floor(buildno / (10 ** Math.abs(i - 6))) % 10).toString(), [tubeOrg[0] + 3.5 * tubeScale * (i - 6), tubeOrg[1]], tubeScale))
}

drawLines(allLines)
```

## Curves

### catmullRom(points, steps = 1000)

**Parameters:**
- `points` ([number, number][]): An array of points through which the curve should pass.
- `steps` (number, optional): The number of steps to divide the curve into. Defaults to 1000.

**Returns:** A polyline ([number, number][]) that represents the Catmull-Rom spline through the given points.

**Description:** 

Generates a [Catmull-Rom spline](https://en.wikipedia.org/wiki/Centripetal_Catmull%E2%80%93Rom_spline), which is a type of interpolating curve, passing through a series of control points. The `steps` parameter controls the smoothness of the curve, with higher values resulting in a more detailed curve.

**Example:**

```js
bt.catmullRom([[0, 0], [10, 15], [20, 5]], 100); // Returns a polyline with 100 points forming a smooth curve through the specified points
```

### nurbs(points, ops = { steps: 100, degree: 2})

**Parameters:**
- `points` ([number, number][]): An array of control points for the NURBS curve.
- `ops` (object, optional): Configuration options for the NURBS curve.
  - `steps` (number): The number of steps to divide the curve into. Defaults to 100.
  - `degree` (number): The degree of the NURBS curve. Defaults to 2.

**Returns:** A polyline ([number, number][]) that represents the NURBS curve through the given points.

**Description:** 

Generates a [Non-Uniform Rational B-Spline (NURBS)](https://en.wikipedia.org/wiki/Non-uniform_rational_B-spline) curve, which provides great flexibility and precision in modeling curves. The `steps` parameter controls the smoothness of the curve, and the `degree` parameter defines the curve's degree, affecting its complexity and how tightly it fits to the control points.

**Example:**

```js
bt.nurbs([[0, 0], [10, 15], [20, 5]], { steps: 50, degree: 3 }); // Returns a polyline forming a NURBS curve with specified degree and steps
```

<!--
### svgToPolylines(svg: string)

**Parameters:**
- `svg` (string): An SVG path string to be converted into polylines.

**Returns:** An array of polylines ([number, number][][]), where each polyline corresponds to a path in the SVG.

**Description:** 

Converts SVG path data into an array of polylines. 

**Example:**

```js
bt.svgToPolylines(`<svg><path d="M0,0 L10,10 Q15,15 20,5" /></svg>`); // Returns an array of polylines representing the SVG path
```
-->

## Randomness

### rand()

**Returns:** A random number between 0 and 1.

**Description:** 

Generates a random floating-point number between 0 (inclusive) and 1 (inclusive). This function does not require any parameters and provides a quick way to introduce randomness into your drawing or modifications.

**Example:**

```js
bt.rand(); // Might return 0.123456789
```

### randInRange(min, max)

**Parameters:**
- `min` (number): The minimum value (inclusive).
- `max` (number): The maximum value (inclusive).

**Returns:** A random number between `min` and `max`.

**Description:** 

Generates a random floating-point number within a specified range. The function takes two parameters: the minimum value (inclusive) and the maximum value (inclusive), and returns a random number within this range.

**Example:**

```js
bt.randInRange(10, 20); // Might return 15.6789
```

### randIntInRange(min, max)

**Parameters:**
- `min` (number): The minimum value (inclusive).
- `max` (number): The maximum value (inclusive).

**Returns:** A random integer between `min` and `max`.

**Description:** 

Generates a random integer within a specified range. This function is similar to `randInRange` but ensures the returned value is an integer. The `max` value is inclusive, making the range of possible outcomes slightly wider.

**Example:**

```js
bt.randIntInRange(1, 10); // Might return 7
```

### setRandSeed(seed)

**Parameters:**
- `seed` (number): A seed value to initialize the random number generator.

**Returns:** Nothing.

**Description:** 

Initializes the random number generator with a specific seed. This function is useful for creating repeatable sequences of random numbers. Setting the same seed value will reset the random number generator to produce the same sequence of numbers.

**Example:**

```js
bt.setRandSeed(12345);
```

### noise(input, options = { octaves, falloff })

**Parameters:**
- `input` (number | [number, ?number, ?number]): A single number or an array representing the coordinates (x, [y], [z]) in n-dimensional noise space.
- `options` (object, optional): Configuration options for noise generation
  - `octaves` (number [0 to 8]): The number of octaves of noise to generate. More octaves produce more detailed noise at the cost of performance.
  - `falloff` (number [0 to 100]): The rate at which the noise detail decreases across octaves.

**Returns:** A noise value between -1 and 1 based on the input coordinates and options.

**Description:** 

Generates Perlin noise or simplex noise based on the input coordinates and configuration options. This function can produce noise in one, two, or three dimensions and is configured by the number of octaves and the falloff rate. It's useful for generating natural-looking textures, landscapes, or other organic variations.

**Example:**

```js
bt.noise(0.5);
bt.noise([0.5, 2.4]);
bt.noise([0.5, 2.4, 3]);
bt.noise(0.5, { octaves: 4, falloff: 50 }); // Might return 0.3425
bt.noise([0.5, 1.2], { octaves: 3, falloff: 75 }); // Might return -0.5687
```

<!--
  
## Easing Curves

### bezierEasing(startY, controlPt0, controlPt1, endY)

**Parameters:**
- `startY` (number): The starting Y value of the Bezier curve.
- `controlPt0` ([number, number]): The first control point as a 2D coordinate `[x, y]`, influencing the curve's shape.
- `controlPt1` ([number, number]): The second control point as a 2D coordinate `[x, y]`, influencing the curve's shape.
- `endY` (number): The ending Y value of the Bezier curve.

**Returns:** A function that, when given an X value between 0 and 1, returns the corresponding Y value on the Bezier curve defined by the input parameters.

**Description:** 

Creates a Bezier easing function based on the provided start and end Y values and two control points. 
This function is useful for generating smooth, customizable easing curves for interpolations between two values. 
The returned function maps an input X (ranging from 0 to 1) to a Y value on the Bezier curve.

**Example:**

```js
const ease = bt.bezierEasing(0, [0.25, 0.1], [0.25, 1], 1);
const y = ease(0.5); // Returns the Y value at X=0.5 on the Bezier curve
```

-->

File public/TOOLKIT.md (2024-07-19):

# The Toolkit  

> This is a quick reference sheet. For <a href="/docs">full documentation refer to this</a>.

> For an introduction to Blot check out <a href="/editor?guide=start">this guide</a>. 

> Check out our <a href="https://www.youtube.com/watch?v=d1noJNmfvC0">38 second trailer for a brief overview of the whole Blot project.</a>

There are three names that provide functionality available in the Blot editor:
`setDocDimensions`, `drawLines`, and `blotToolkit` (which can also be referenced as `bt`).

The first two affect the drawing environment itself, and the `blotToolkit` is used for creating line drawings.

## Environment Affecting

```js
setDocDimensions(width: number, height: number)
drawLines(polylines: [number, number][][])
```

## Modify Polylines

Take and modify polylines in place returns first passed polylines.

These functions are available in the `blotToolkit` or `bt` object.

```js
bt.iteratePoints(polylines, (pt, t) => { ... }) // return pt to modify, "BREAK" to split, "REMOVE" to filter out point
bt.scale(polylines, scale : scaleXY | [scaleX, scaleY], ?origin: [ x, y ]) 
bt.rotate(polylines, degrees, ?origin: [ x, y ]) 
bt.translate(polylines, [dx, dy], ?origin: [ x, y ]) 
bt.originate(polylines) // moves center to [0, 0] 
bt.resample(polylines, sampleRate) 
bt.simplify(polylines, tolerance) 
bt.trim(polylines, tStart, tEnd)
bt.merge(polylines)  
bt.join(polylines0, ...morePolylines) 
bt.copy(polylines)
bt.cut(polylines0, polylines1) 
bt.cover(polylines0, polylines1) 
bt.union(polylines0, polylines1)
bt.difference(polylines0, polylines1)
bt.intersection(polylines0, polylines1)
bt.xor(polylines0, polylines1)
bt.offset(polylines, delta, ?ops = { endType, joinType, miterLimit, arcTolerance })
```

## Get Data From Polylines

These functions are available in the `blotToolkit` or `bt` object.

```js
// take polylines return other
bt.getAngle(polylines, t: [0 to 1]) // returns angle in degrees
bt.getPoint(polylines, t: [0 to 1]) // returns point as [x, y]
bt.getNormal(polylines, t: [0 to 1]) // returns normal vector as [x, y]

bt.pointInside(polylines, pt)

bt.bounds(polylines) 
/*
returns { 
  xMin, xMax, 
  yMin, yMax, 
  lt, ct, rt, 
  lc, cc, rc,
  lb, cb, rb,
  width, height
}

l is left
c is center
r is right
t is top
b is bottom

they are arranged in this configuration around the bounding box of the polylines

lt--ct--rt
 |   |   |
lc--cc--rc
 |   |   | 
lb--cb--rb
*/
```

## Generate Polylines

These functions are available in the `blotToolkit` or `bt` object.

```js
const myTurtle = new bt.Turtle()
  .forward(distance: number)
  .arc(angle: number, radius: number)
  .goTo( [ x: number, y: number ] ) // move with up/down state
  .jump( [ x: number, y: number ] ) // move but don't draw
  .step( [ dx: number, dy: number ] ) // add delta to turtles current position
  .right(angle: number)
  .left(angle: number)
  .setAngle(angle: number)
  .up() // sets drawing to false
  .down() // sets drawing to true
  .copy()
  .applyToPath(fn) // takes (turtlePath) => { }
  .lines() // get copy of the Turtle's path

// data
const position = myTurtle.pos // [x: number, y: number]
const angle = myTurtle.angle // number
const path = myTurtle.path // is array of polylines [number, number][][]
const drawing = myTurtle.drawing // boolean
```

```js
bt.catmullRom(points, ?steps = 1000) // returns polyline [number, number][]
bt.nurbs(points, ?ops = { steps: 100, degree: 2}) // returns polyline [number, number][]
```

<!-- 
```js
bt.svgToPolylines(svg: string) // returns array of polylines [number, number][][]
``` 
-->

## Randomness

These functions are available in the `blotToolkit` or `bt` object.

```js
bt.rand();

bt.randInRange(min: number, max: number);

bt.randIntInRange(min: number, max: number); 

bt.setRandSeed(seed: number);

bt.noise(
  number | [ x:number , ?y: number , ?z: number ], 
  { 
    octaves: number [0 to 8], 
    falloff: number [0 to 100] 
  }
);
```

## Idioms

These are small useful code snippets.

```js
function centerPolylines(polylines, documentWidth, documentHeight) {
  const cc = bt.bounds(polylines).cc;
  bt.translate(polylines, [documentWidth / 2, documentHeight / 2], cc);
}
```

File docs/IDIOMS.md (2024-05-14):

# Idioms

Useful common patterns.

### Imports in One Line

```js
const { Turtle, trim, merge, cut, cover, rotate, scale, translate, originate, iteratePoints, pointInside, resample, join, copy, union, difference, intersection, xor, getAngle, getPoint, getNormal, bounds, nurbs, catmullRom, svgToPolylines, rand, setRandSeed, randInRange, randIntInRange, noise } = toolkit;

```

### Displace Along Normal

```js
const w = 125;
const h = 125;

setDocDimensions(w, h);

const noisyCircle = new tk.Turtle()
  .arc(360, 26)
  .apply(turtle => {
    const pls = turtle.path;
    tk.resample(pls, .1);
    tk.iteratePoints(pls, (pt, t) => {
      const [x, y] = pt;
      let freq = 1.5;
      const mag = Math.sin(t*18*Math.PI*2)*2;
      const norm = tk.getNormal(pls, t);

      return [
        x + norm[0]*mag,
        y + norm[1]*mag
      ]
    })
  })
  .path;

tk.originate(noisyCircle);

drawLines(noisyCircle);
```

### Displace Along Angle

```js
const w = 125;
const h = 125;

setDocDimensions(w, h);

const noisyCircle = new tk.Turtle()
  .arc(360, 26)
  .apply(turtle => {
    const pls = turtle.path;
    tk.resample(pls, .05);
    tk.iteratePoints(pls, (pt, t) => {
      const [x, y] = pt;
      let freq = 1.5;
      const mag = tk.noise([x*freq, y*freq])*2;
      const angle = (tk.getAngle(pls, t)+90)/180*Math.PI;

      return [
        x + Math.cos(angle)*mag,
        y + Math.sin(angle)*mag
      ]
    })
  })
  .path;

tk.originate(noisyCircle);

drawLines(noisyCircle);
```

### Poisson-Disc Sampling (thanks to Reinder Nijhoff)

```js
function createPoissonDisc(radius) {
  let cellSize = 1 / Math.sqrt(2) / radius;
  let cells = [];
  let queue = [];

  insert(p) {
    const x = p[0] * cellSize | 0;
    const y = p[1] * cellSize | 0;
    for (let xi = x - 1; xi <= x + 1; xi++) {
      for (let yi = y - 1; yi <= y + 1; yi++) {
        const ps = this.cell(xi, yi);
        for (let i = 0; i < ps.length; i++) {
          if ((ps[i][0] - p[0]) ** 2 + (ps[i][1] - p[1]) ** 2 < (ps[i][2] + p[2]) ** 2) {
            return false;
          }
        }
      }
    }
    queue.push([p, x, y]);
    if (queue.length > (10 * radius + 1) | 0) {
      const d = queue.shift();
      this.cell(d[1], d[2]).push(d[0]);
    }
    return true;
  }
  cell(x, y) {
    const c = cells;
    return (c[x] ? c[x] : c[x] = [])[y] ? c[x][y] : c[x][y] = [];
  }

  return {
    cell,
    insert
  };
}
```

### Circle

```js
function circle(r) {
  const t = new tk.Turtle();
  t.arc(360, r);
  const cc = tk.bounds(t.path).cc;
  tk.translate(t.path, [0, 0], cc);

  return t.path;
}
```

### Rectangle

```js
function rect(w, h) {
  return [
    [-w/2, h/2],
    [-w/2, -h/2],
    [w/2, -h/2],
    [w/2, h/2],
    [-w/2, h/2],
  ]
}
```

### Length

```js
function length([x0, y0], [x1, y1]) {
  return Math.sqrt((x1 - x0) ** 2 + (y1 - y0) ** 2)
}
```

Hatching

```js
```

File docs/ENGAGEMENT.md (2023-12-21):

# Getting a Blot

Blot is a "you ship, we ship" project. That means we will send the machine to people you build projects with the machine. And the way to start this engagement is just by getting started building.

A well designed "you ship, we ship" should feel like everyone is contributing to a coherent project while not having contributors be dependent on each other. Each contribution is self-contained and satisfying to develop on its own but the aggregate results in something greater than the sum of its parts.

With Sprig we didn't just build a DIY Gameboy, we built a whole library of games. A new class of console where everyone that plays it helped build it.

With Haxidraw we know what we are going to ship you, but we don't know what you will ship us or what we are building together.

Let's explore some ideas to address this.

## A MOMA Exhibit

Let's create a collectively developed physical/digital art exhibit for the Museum of Modern Art in NYC.

Hack Club will produce a microworld web-based environment for creating generative line drawings which can be fabricated on the Blot. We will encourage students to create a collection of digital art which can be submitted to our virtual or AR gallery space where they can see their work alongside pieces created by thousands of teens around the world. When they have curated their own exhibit (collection) in this virtual gallery we send them a machine so they can run a physical pop-up exhibit in their high school, printed using the haxidraw machines that they have assembled. We will do this for one year.

After that year, we will host a physical installation of these pop-up exhibits at a museum we partner with and fly out many contributors from around the world to celebrate their collective creation together.

There are a couple units of interaction with this model.

- an art piece
- a collection
  - a parametric art generator
- a drawing machine
- a pop-up exhibit
- the grand museum piece

## Art Piece



Design a digital art piece. You can draw it or generate it algorithmically.

Explore all the art in Hack Clubs virtual museum of plotter art.

VIRTUALARTEXHIBITION2-300x230

## Collection

Make several pieces which are thematically connected.

automata-1

This could be done manually or with a program which parametrically generates art.

Submit this collection to our virtual museum to receive a Blot kit.

## Drawing Machine

Assemble your machine.



## Pop-Up Exhibit

Use your machine to fabricate the art you designed.



Host an exhibit in a local venue like your school or a makerspace.

## The Museum

Come celebrate with the community as we turn our virtual museum into a real one and share it with the world.

download

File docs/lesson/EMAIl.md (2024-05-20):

Subject:

```
Need something after AP exams?
```

Body:

```

Hi,

At [Hack Club](https://hackclub.com/), we build tools to help students worldwide practice coding and engineering skills by creating inspiring projects. This past year, we developed a drawing robot called [Blot](https://blot.hackclub.com), which we’ll send to any high schooler for free when they code an art piece in our web-based programming environment.

We believe the best way to cap off a year of learning AP CS material is with a project that lets students apply their knowledge to create tangible results.

![Blot Image](https://blot.hackclub.com/assets/blot-clear-bg.webp)

Blot is part of our “You Ship, We Ship” program. When students create projects with our tools and share them publicly, we send them physical engineering kits. Blot was developed with support from MIT’s Center for Bits and Atoms and is funded by donors like Tom Preston-Werner, the founder of GitHub.

You can find an example lesson plan for using Blot in your classroom here: [hack.af/learnblot](https://hack.af/learnblot).

Through drawing projects students can practice logic branching, function calls, one and two-dimensional arrays, and recursive algorithms.

Additionally, we offer another project called [Sprig](https://sprig.hackclub.com), where students can program tile based games in JavaScript. When they share their games with us, we send them the materials to build a handheld console to play those games.

If you’d like posters for Blot and Sprig for your classroom, you can [sign up to receive them here](https://airtable.com/appv0BzBY2APyIXj6/shrk2RTYPbpM1KlKF). We’d also love your feedback on how these tools can fit into your curriculum.

Best regards,

Zach
Founder of Hack Club

P.S. I’ve cc'd Leo, the creator of Blot and Sprig.
```

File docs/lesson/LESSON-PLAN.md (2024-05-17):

# Blot Lesson Plan

Here is an example lesson plan on how to run Blot in your classroom. It could be as short as one day or extended over several weeks. To use Blot in multiple classes set the goal of each student creating their own artwork and submitting it to receive a Blot drawing robot.

For a one day schedule:

- Introduce Blot and Hack Club to your class [5 minutes]
  - Get familiar with the Blot editor
  - Make a simple shape together
- Learn different levels of drawing techniques [20 minutes]
  - Work through Square Disarray guide
  - Work through feather guide   
- Work through the Blot visual puzzles [25+ minutes]

# Introduction

For the quickest introduction check out this video trailer for Blot.

(https://www.youtube.com/watch?v=d1noJNmfvC0)

[Watch the Blot Trailer Here](https://www.youtube.com/watch?v=d1noJNmfvC0)

Blot is a gateway to making physical things with machines through programmatic art. The process starts by using JavaScript in a web-based editor to create a line drawing that is generated with code. When you submit the line drawing to the virtual gallery Hack Club will send you the parts to build a drawing robot. That drawing robot can then draw your line drawing in real life. Check out this video to get a sense of the creative process and to see Blot in action.

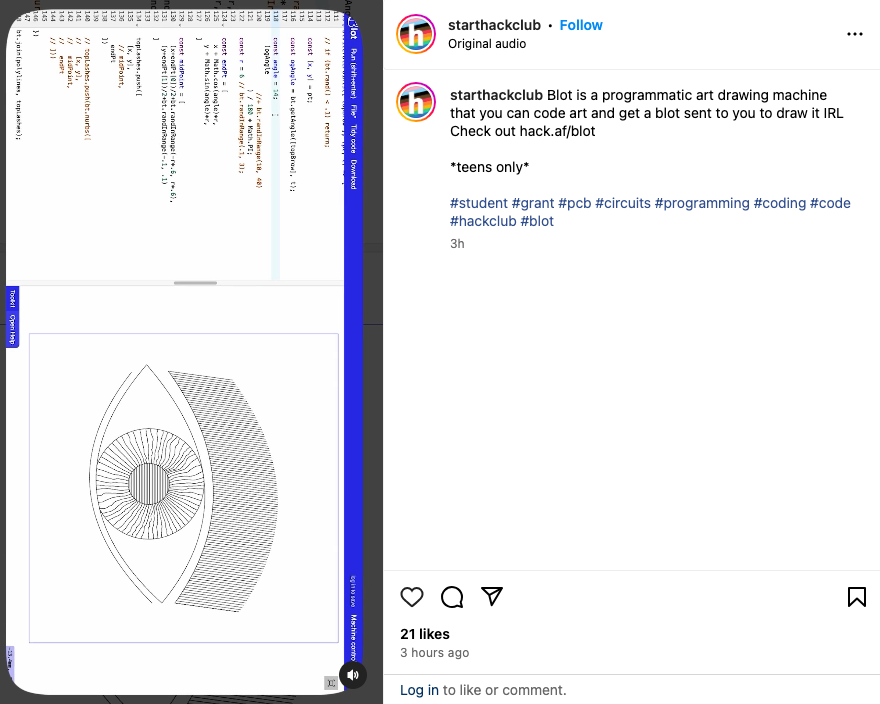
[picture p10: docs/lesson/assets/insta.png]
(https://www.instagram.com/reel/C7CPejLAwc0/?hl=en)


[See what you can make in Blot here.](https://www.instagram.com/reel/C7CPejLAwc0/?hl=en)

Blot is made by Hack Club and is free to participate in to teenagers all over the world. We’re on a mission to create high quality publicly available engineering tools which inspire young people to pursue projects they didn’t know were possible. We’re funded by donors like the founder of GitHub who allow us to provide these tools to the world for free. Everything we make is open-source. That means it’s built in public (with teenage contributors) and every aspect of the project from the [hardware and electronics to the web editor and finances is online in the open](www.github.com/hackclub/blot).

### Getting in the Editor

This video will orient you to the Blot editor and demonstrate the most basic Blot drawing.

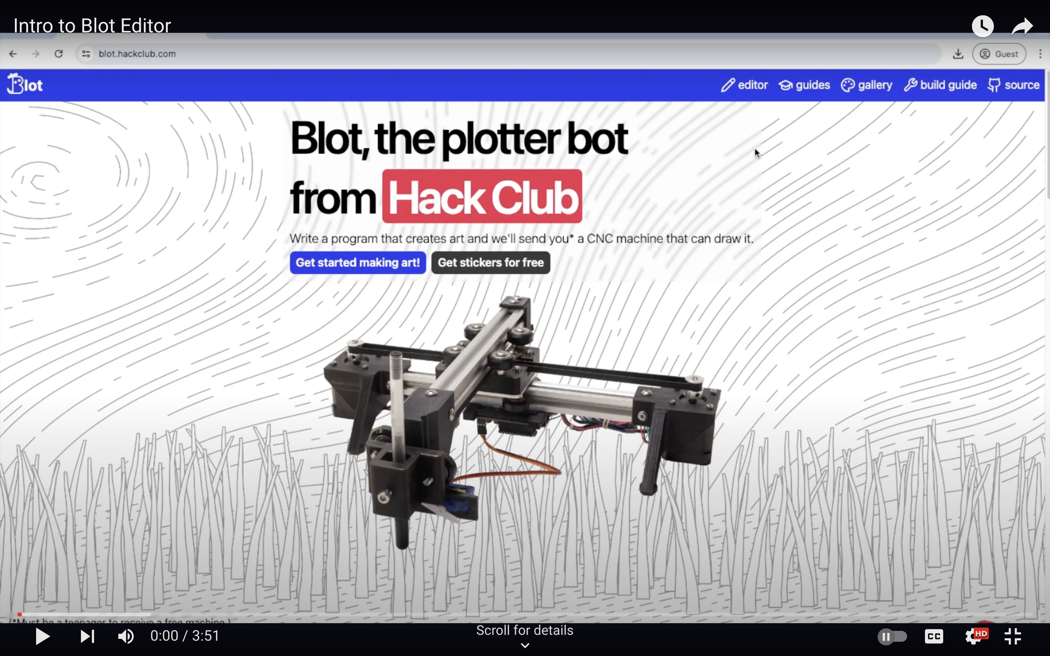
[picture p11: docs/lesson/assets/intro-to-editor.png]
(https://youtu.be/OZ9KaFr1V_o)


[Editor Intro Video Here](https://youtu.be/OZ9KaFr1V_o)

To start head over to:

```
https://blot.hackclub.com/editor
```

You'll see this window:

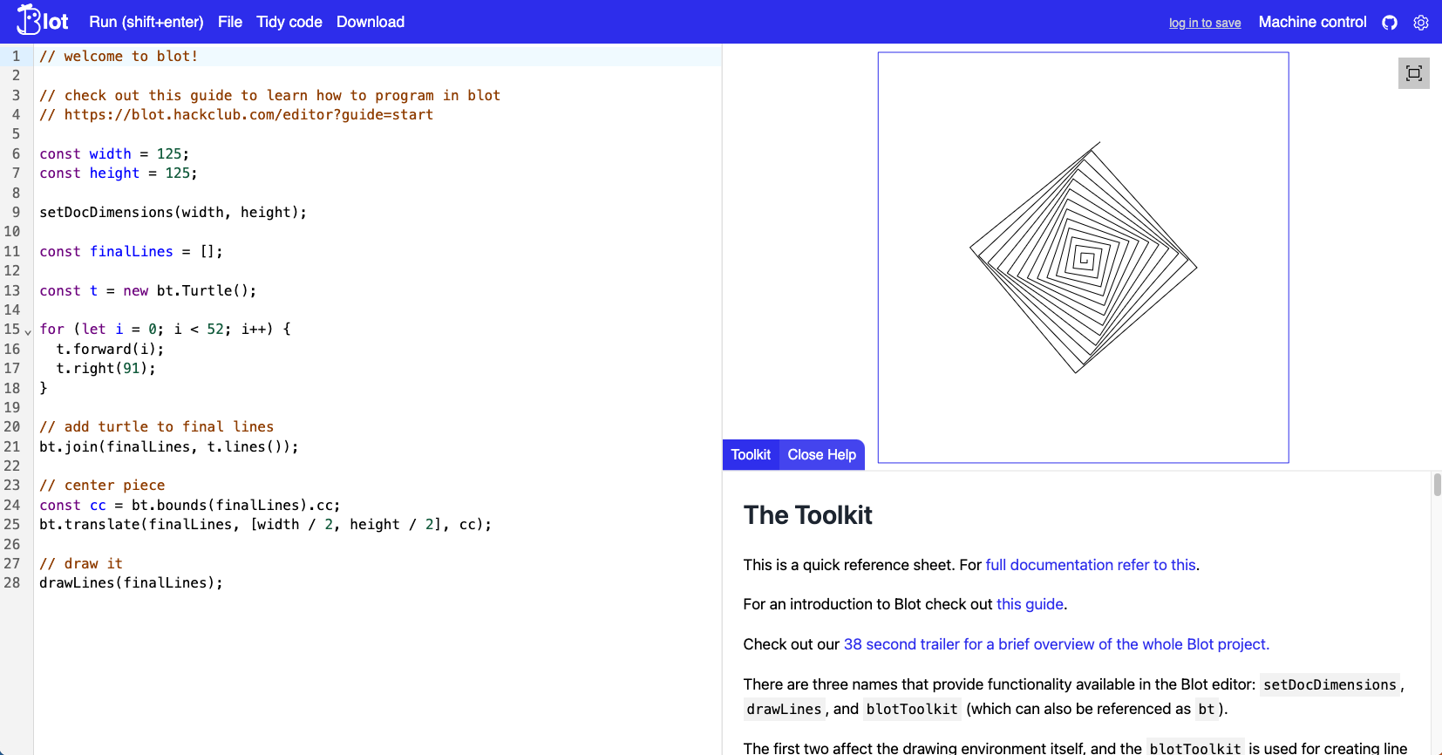
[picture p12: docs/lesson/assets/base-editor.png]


We recommend making an account to save your files in the cloud. You’ll just need an email.

Click `log in to save`

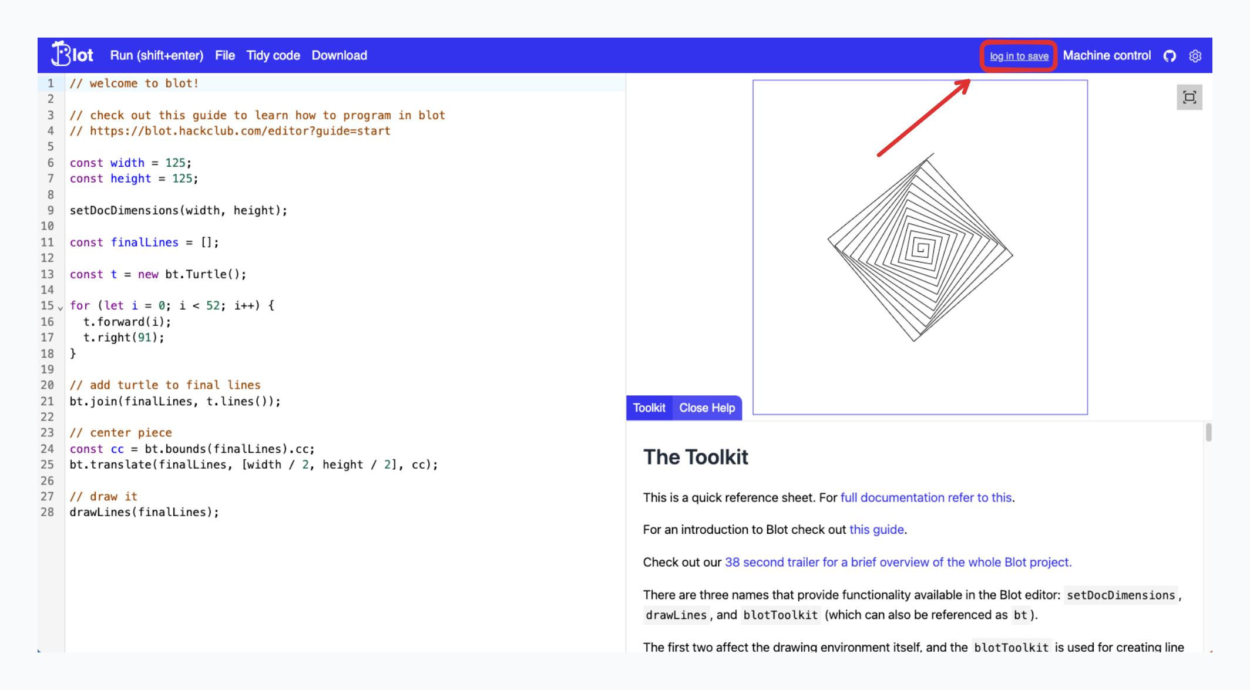
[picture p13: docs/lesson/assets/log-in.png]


Your program will live on the left. It's JavaScript.

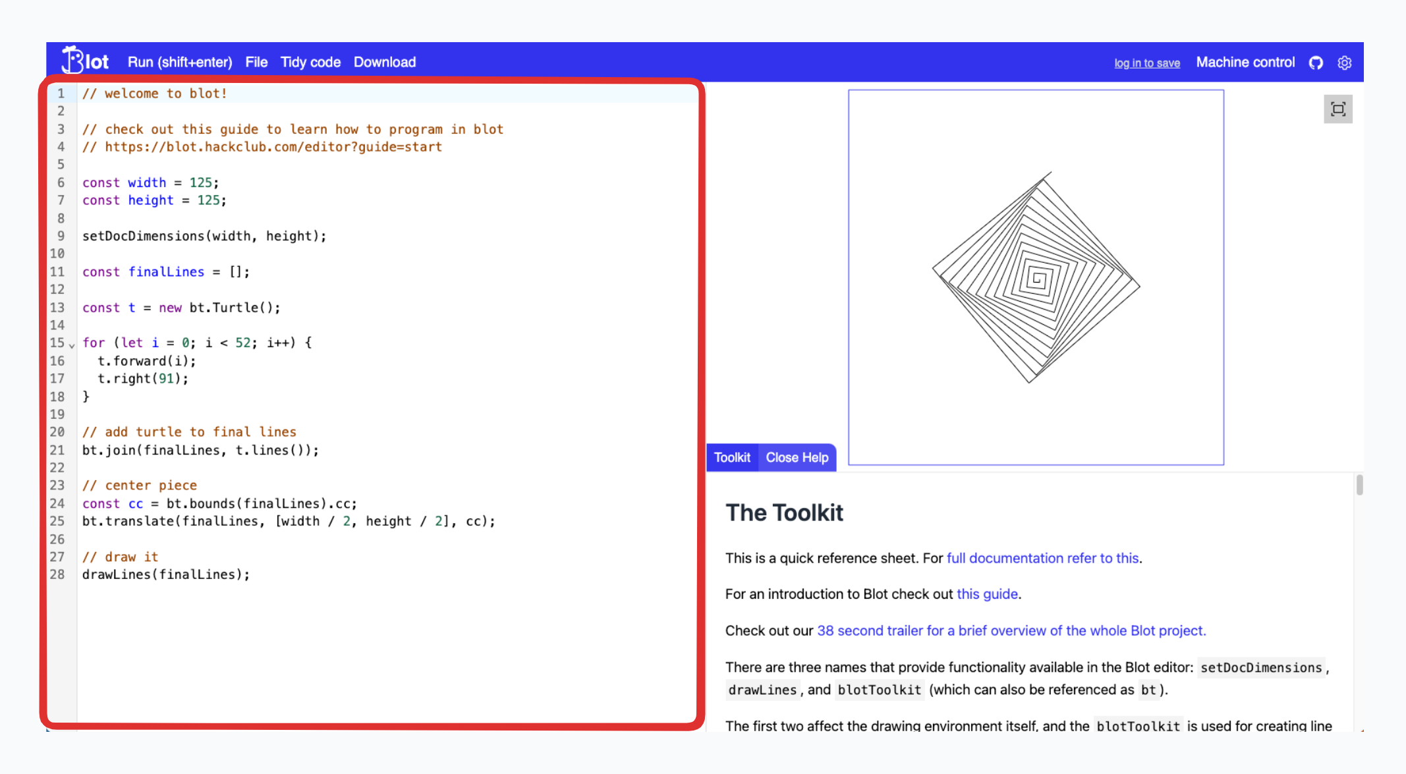
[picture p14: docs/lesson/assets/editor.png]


And the drawing output on the top-right.

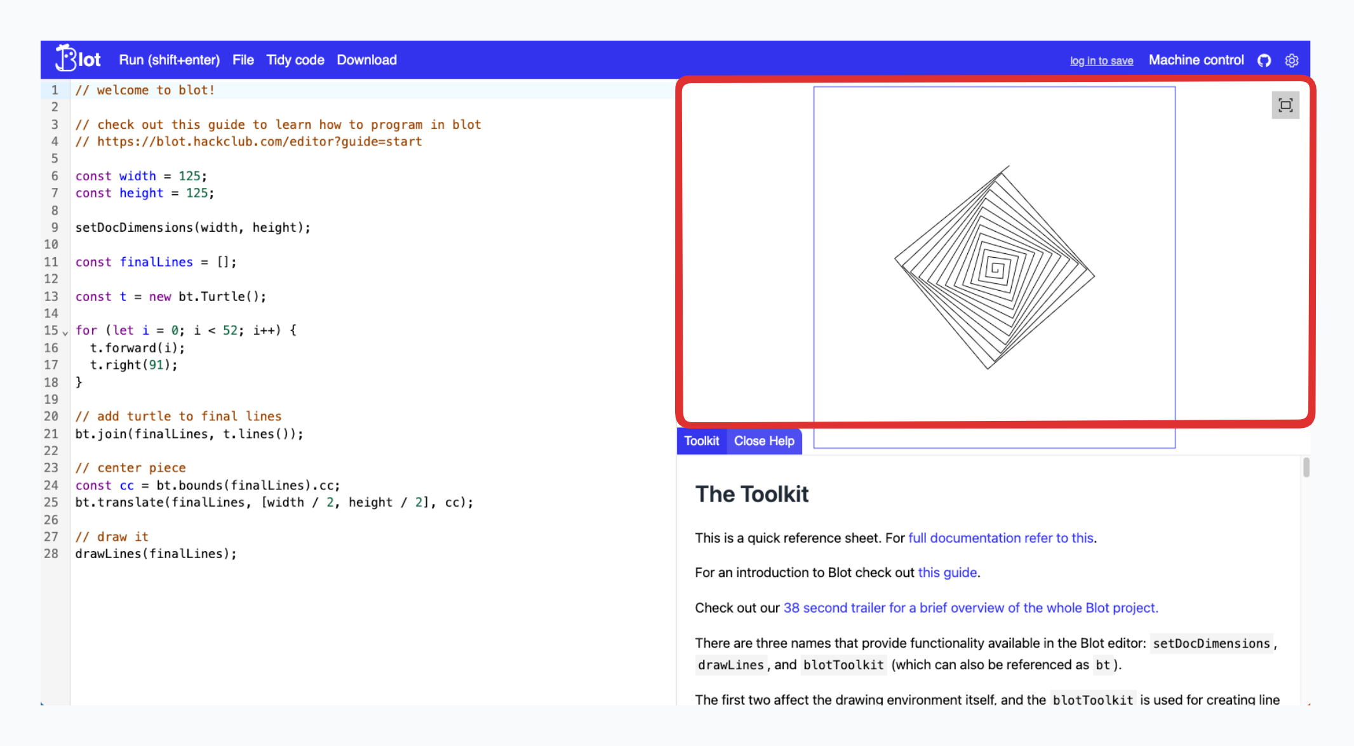
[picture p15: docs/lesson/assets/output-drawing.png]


In the bottom right you can find information about what functions are available in the editor.

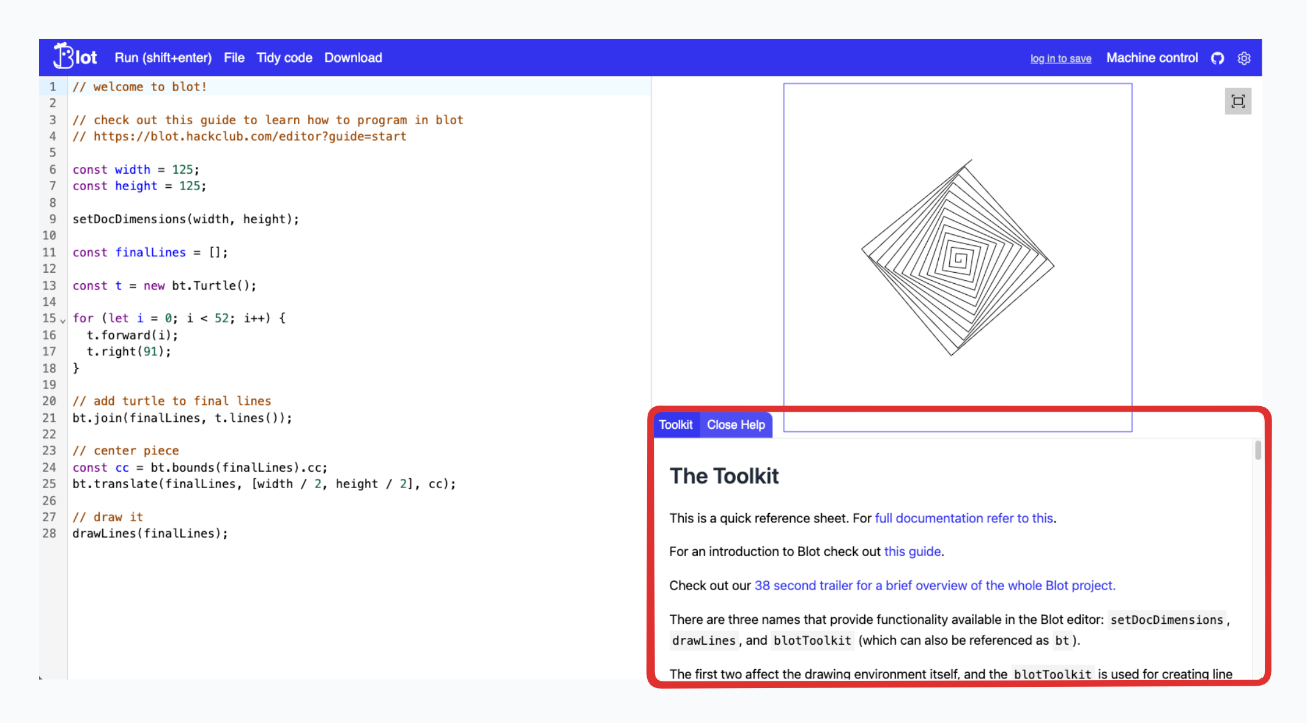
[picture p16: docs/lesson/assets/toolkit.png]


You can run your program by clicking `Run (shift+enter)` or with the hotkey `shift+enter`.

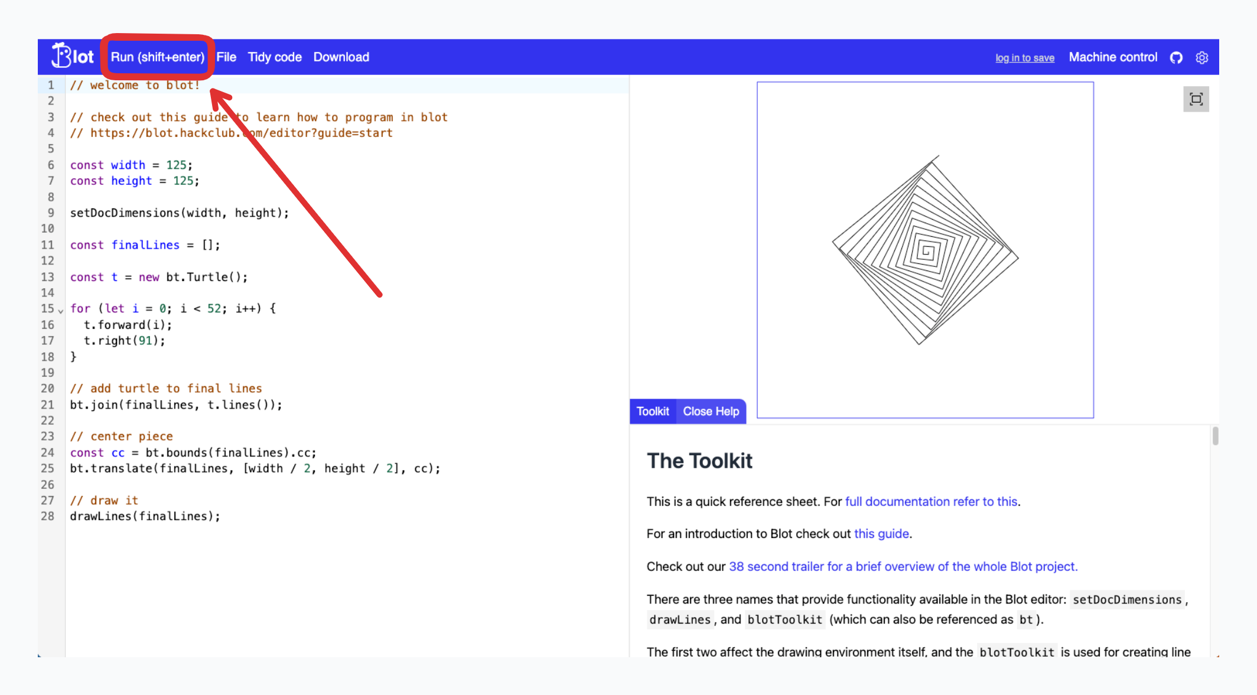
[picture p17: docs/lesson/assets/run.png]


To center the view area on your document you can hit the button in the top right of the view window.

This will only work if you've called `setDocDimensions` in your code.

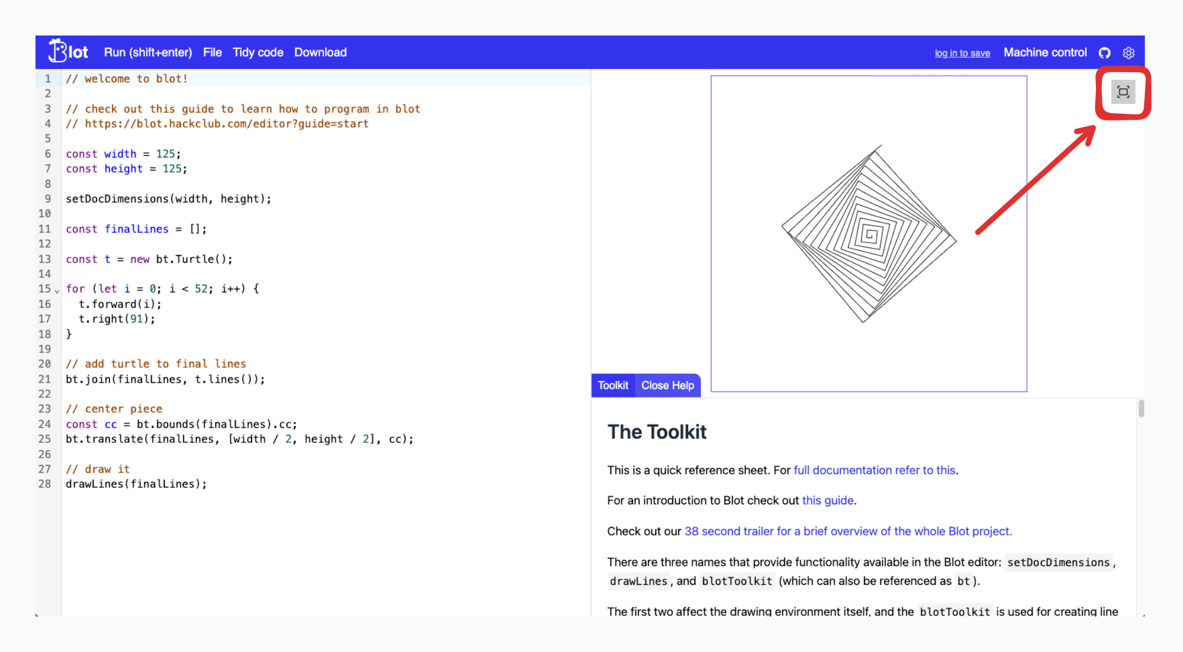
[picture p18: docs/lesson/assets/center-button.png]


If I hover and drag over a number I can watch the drawing update in real time.



To save my document I can got to `File` -> `Save to the cloud`

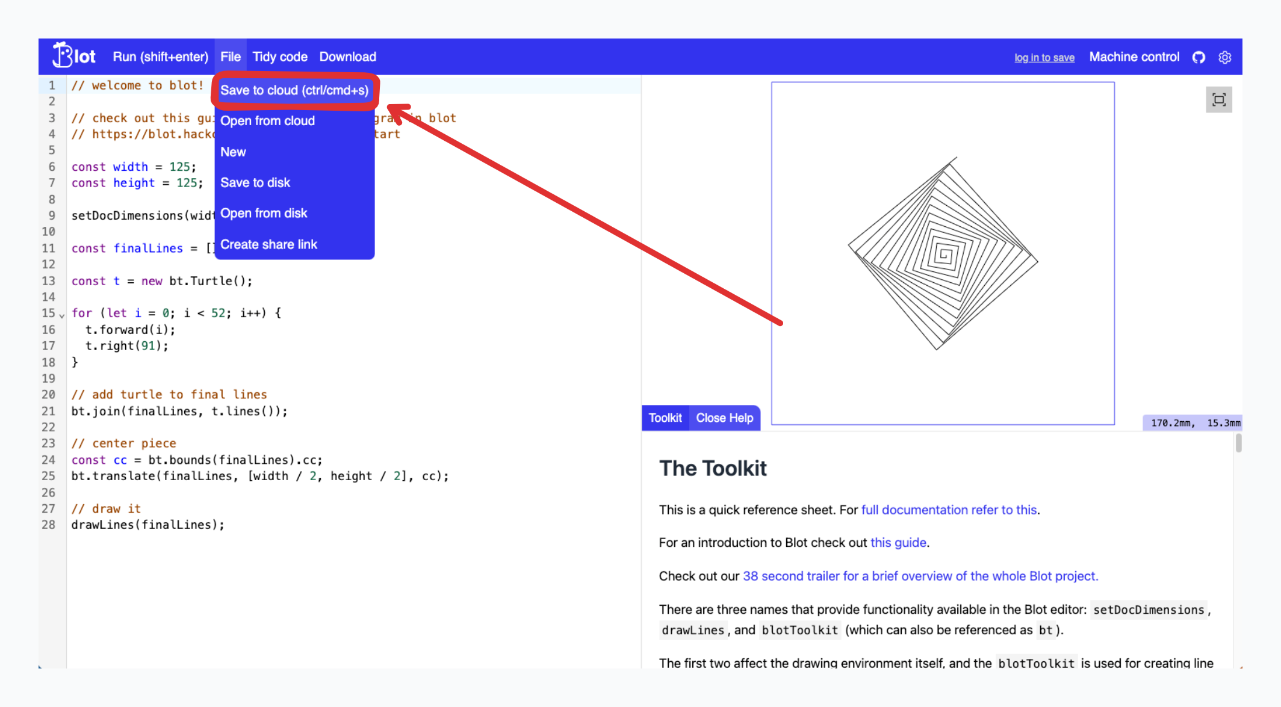
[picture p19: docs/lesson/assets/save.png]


Let’s make some drawings.

# Drawing Techniques

Blot includes a number of drawing functions in the `Toolkit`. Let's familiarize ourself with them by making some drawings.

Below we will walk through two tutorials. 



The first one, `Square Disarray`, we will recreate a classic digital art piece. It is aimed more at beginners and will rely on programming concepts like variables, loops, and functions.



In the second guide,  `Intro to the Blot Toolkit`, we will draw feathers. The guide will cover more of the drawing functions provided in the Blot editor. It will rely on concepts like randomness and mutation.

### Square Disarray

We'll start with drawing inspired by Georg Nees' Cubic Disarray.

Head over to:

```
https://blot.hackclub.com/guides
```

You'll see this page.

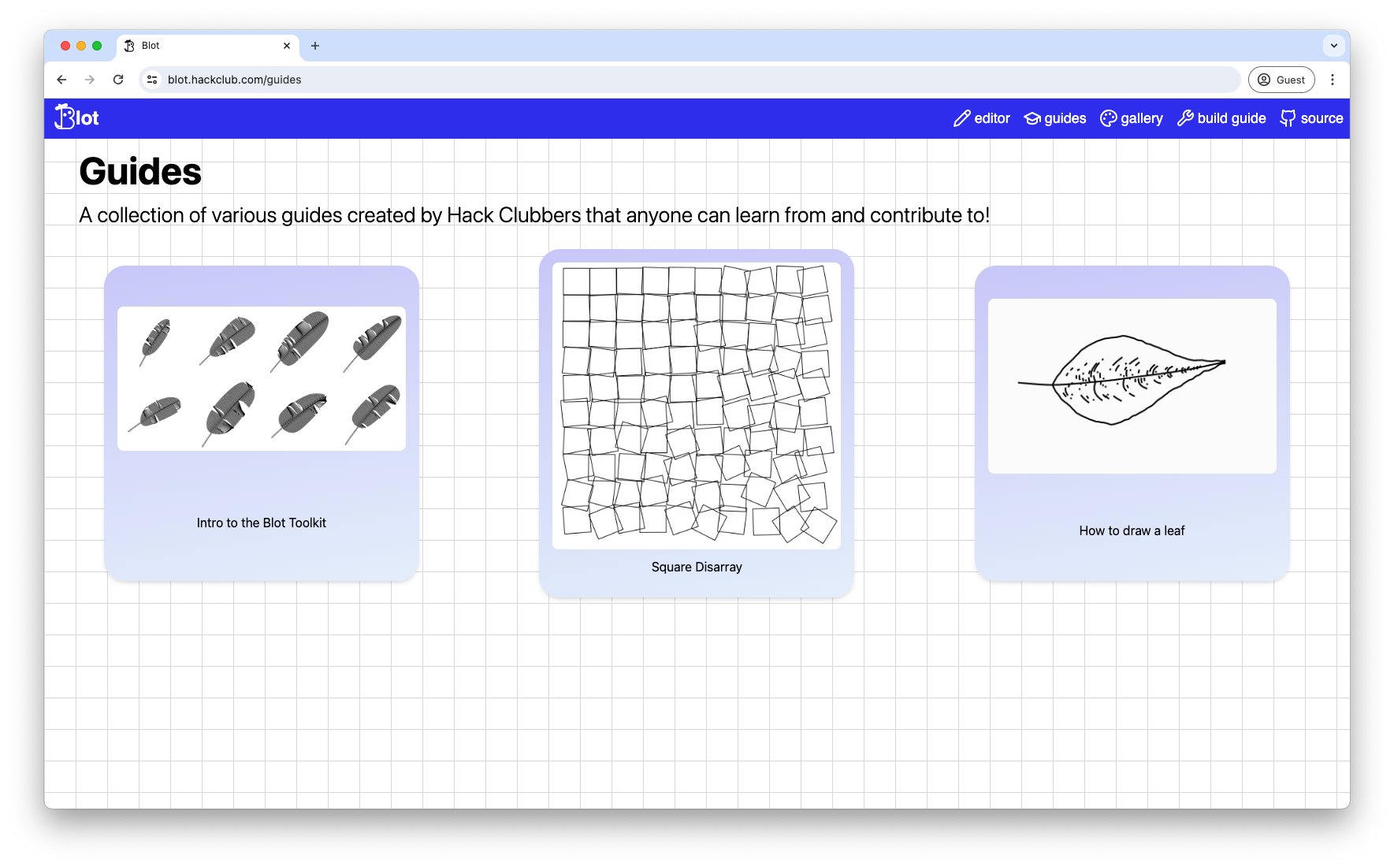
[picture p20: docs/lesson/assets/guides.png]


Open up `Square Disarray`.

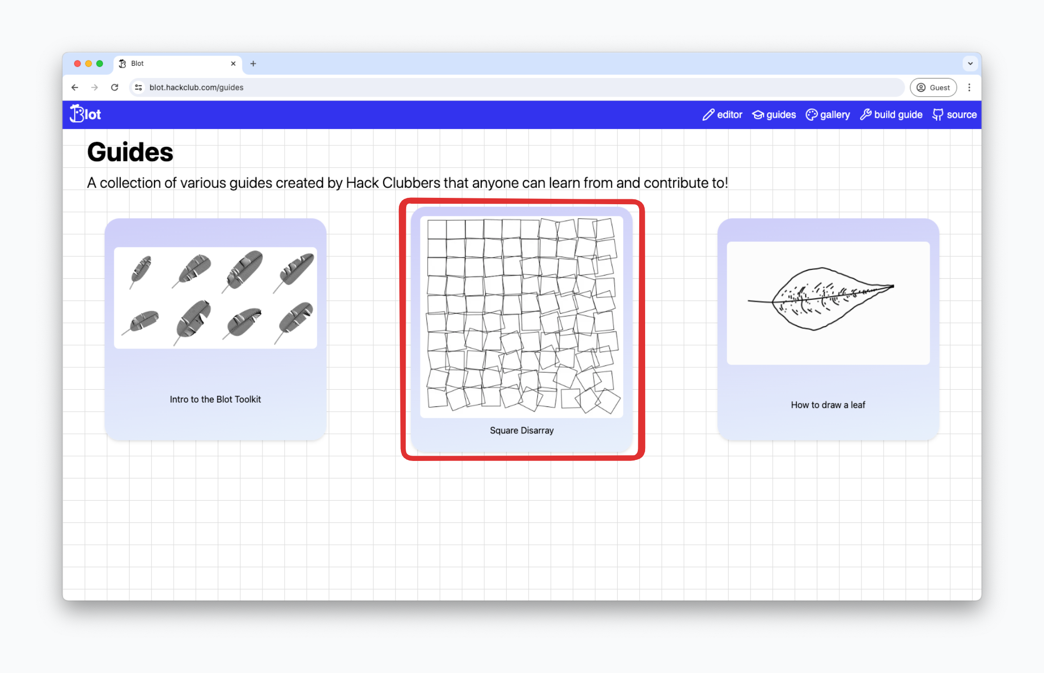
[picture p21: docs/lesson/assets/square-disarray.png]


The editor will ask if you want to reset the code you have cached. Resetting will make it easier to follow along with the guide. Make sure you've saved the code to the cloud if you want to keep it.

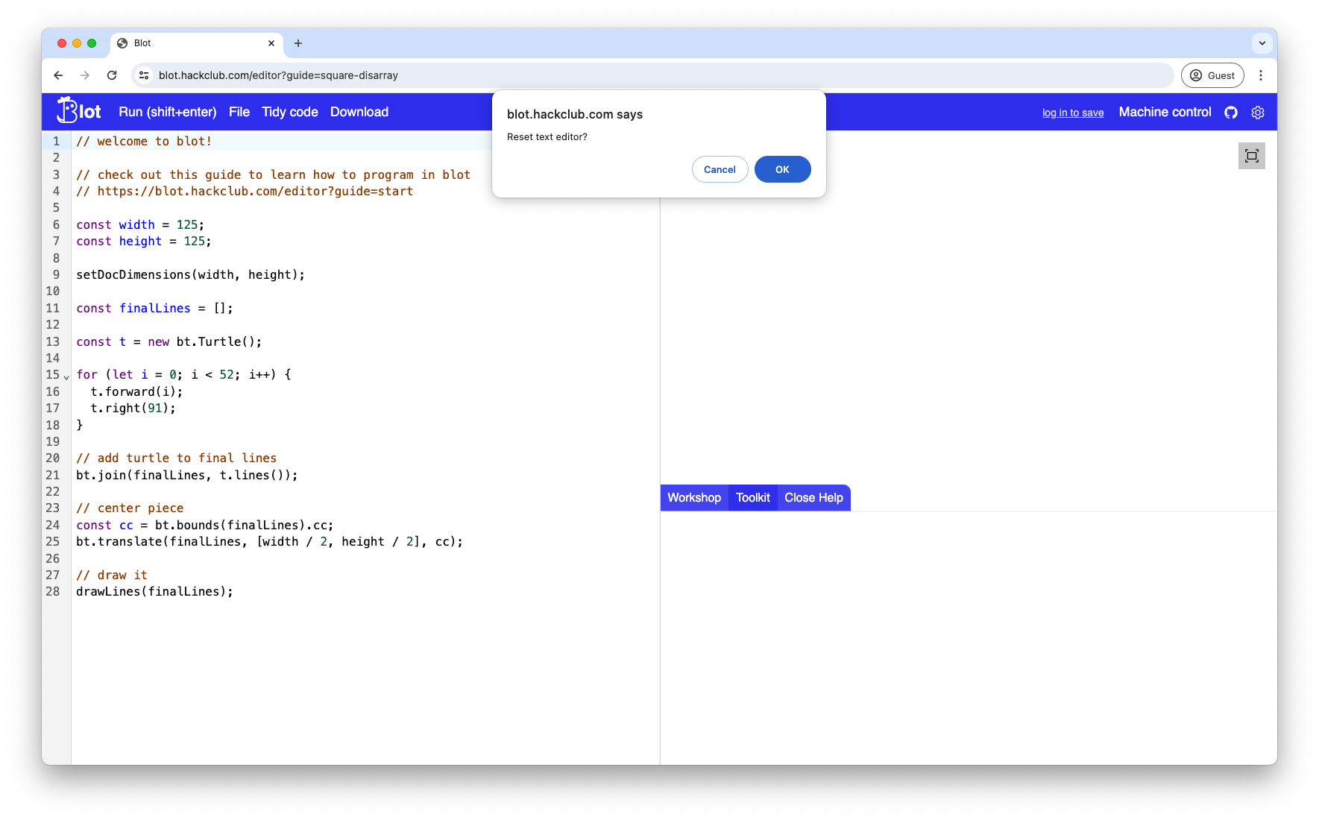
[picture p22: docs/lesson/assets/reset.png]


You'll see a new tab in the bottom right called workshop.

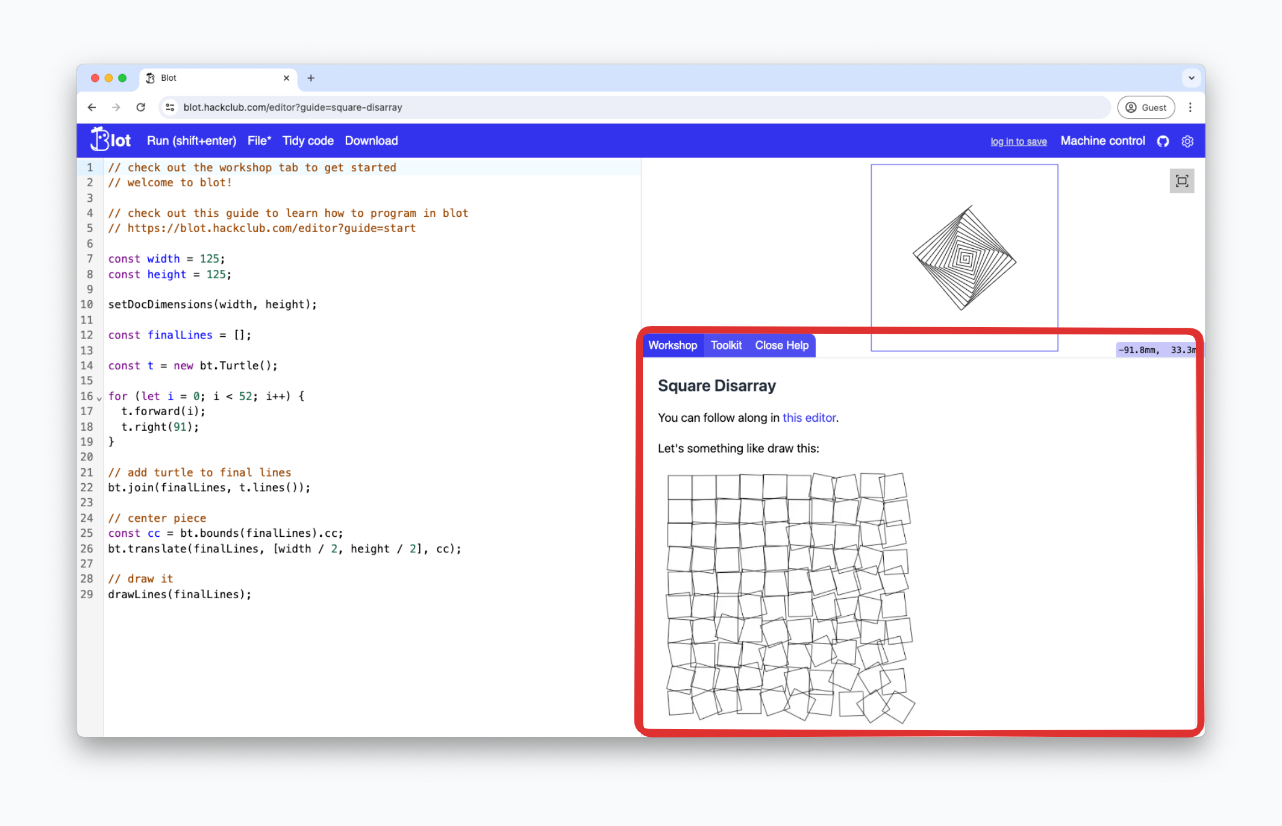
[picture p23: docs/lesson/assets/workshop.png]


Follow along with the guide.

You can find a video of me walking through the Square Disarray below. This will show you how to work through guides in the Blot editor.

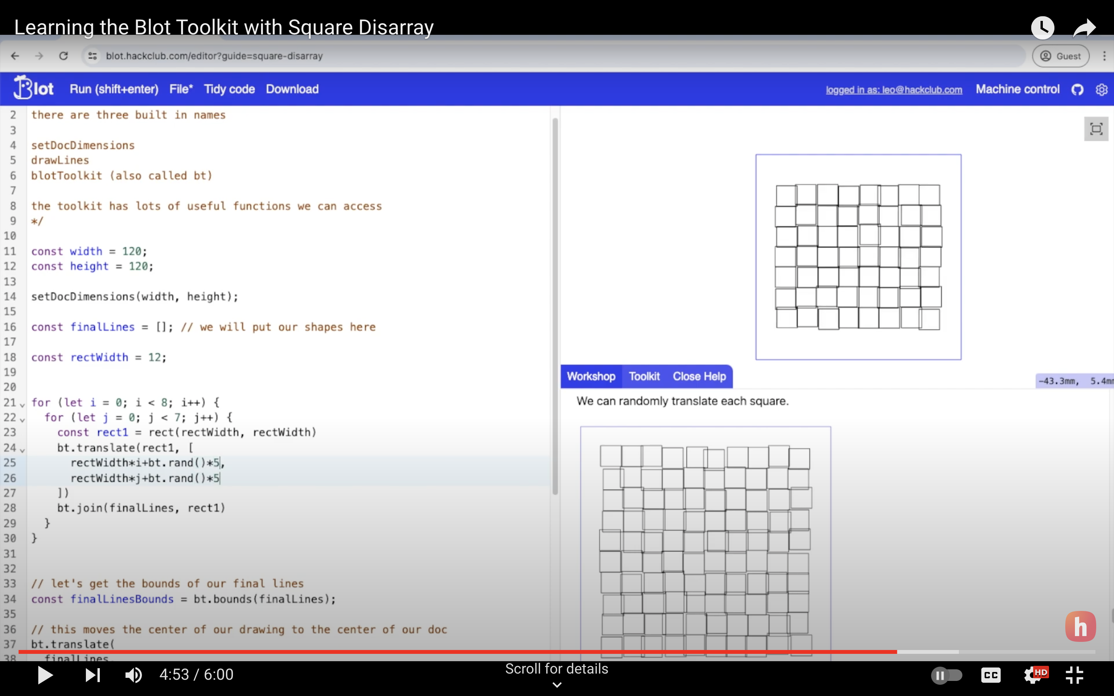
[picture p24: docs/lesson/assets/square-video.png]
(https://youtu.be/mP4rUdaF8ng)


[Watch how to use a guide here.](https://youtu.be/mP4rUdaF8ng)

### Feathers (Intro to the Blot Toolkit)

Head back over to `https://blot.hackclub.com/guides` and select `Intro to the Blot Toolkit`.



Work through the guide in a manner similar to Square Disarray.

# Blot Visual Puzzles

Below are a series of visual puzzles. Try to recreate them.

When you've mastered these try to recreate your favorite piece from [the gallery]().

### 1) A simple rectangle



### 2) Can you make it a function?



### 3) In a row



### 4) All around



### 5) Not so messy



### 6) Round the top



### 7) Round the table



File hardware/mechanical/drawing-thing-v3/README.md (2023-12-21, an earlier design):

# Blot

drawing machine with a turtle illustration

 Blot is a "you ship, we ship" project, similar to [Sprig](https://sprig.hackclub.com). This time if you make some digital art we'll send you the parts to build a robot which can make that art real.

We're also working with some researchers at MIT to make digital fabrication machines like this much more open and hackable. We're doing this by taking functionality which would ordinarily be inaccessible in the firmware and lifting it up to the user in a programmable browser editor. We call it [Modular Things](https://github.com/modular-things/modular-things).

## Model

The [full model can be found here](https://cad.onshape.com/documents/63bea8a7de5a67f20db27d22/w/8d3bc6b2e7a16d7a1133b3b5/e/b415f757fff520875b42c91b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).

## BOM

### 3D Printed Parts

The 3D printed parts are found in [`/stls`](./stls) if you are able to print them yourself. The quantity of each part is listed in the name as such `name_x${QUANTITY}`.

| Part | Quantity | Image | notes |
| --- | --- | --- | ----- |
| Belt clip | 1 | belt clip | |
| Foot | 2 | foot | |
| Motor bracket | 2 | motor bracket | |
| Carriage | 1 | carriage | |
| Idler front | 1 | idler front | |
| Pen holder | 1 | pen holder | |
| Printed rail | 1 | rail | |
| PCB Mount | 1 | <img alt="mount" src="https://cloud-r8rwrwooq-hack-club-bot.vercel.app/0pcbmount.png" | |
| Management Spacer | 1 | <img alt "spacer" src="https://cloud-r8rwrwooq-hack-club-bot.vercel.app/4cablespacer.png" | |

### Electronics

| Part | Quantity | Notes |
| --- | --- | --- |
| Circuit board | 1 | included parts on board are 2 stepsticks, usb-c |
| XIAO RP-2040 development board | 1 | with headers |
| USB-C charger with adapter | 1 | not included (bring your own) |

### Hardware

<!-- todo: add part numbers to mcmaster parts -->
<!-- todo: double check if this parts list is accurate -->

| Line | Part | Quantity | Notes | Source |
| ---- | --- | --- | --- | --- | --- |
| 0 | Flanged bearings (625) | 10 | | [Amazon](https://www.amazon.com/uxcell-Bearing-5x16x5mm-Shielded-Bearings/dp/B07Z3DXF14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) |
| 1 | GT2 timing belt, 6mm width (around 45 in or 110cm in length) | 1 | | [Amazon](https://www.amazon.com/Printing-Zeelo-Fiberglass-Rostock-Printers/dp/B08974S1CC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) |
| 1 | timing belt pulley wheel (12mm dia) | 2 | | [Amazon](https://www.amazon.com/WINSINN-Aluminum-Synchronous-Timing-Printer/dp/B077GNZK3J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) |
| 1 | 2.5mm allen key (M3) | 1 | For M3 button head screw | [McMaster-Carr](https://www.mcmaster.com/allen-keys/l-keys-9/system-of-measurement~metric/size~2-5-mm/) |
| 2 | 1mm spacers 10mm OD | 5 | | [OpenBuilds](https://openbuildspartstore.com/precision-shim-10x5x1mm/) |
| 3 | M5 hex nuts | 25 | | [McMaster-Carr](https://www.mcmaster.com/nuts/metric-medium-strength-steel-hex-nuts-class-8/thread-size~m5/) |
| 4 | M5 t-nuts | 22 | | [Amazon](https://www.amazon.com/Fastener-Nickel-Plated-Sliding-Aluminum-Profile/dp/B086MKNYDS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) |
| 5 | V-wheels | 11 | 8 for the carriage, 3 for pen holder | [Amazon](https://www.amazon.com/V-Shape-Bearing-Accessories-Sliding-Printer/dp/B07NSHH9N4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) |
| 7 | 6mm spacers 10mm OD | 4 | | [McMaster-Carr](https://www.mcmaster.com/spacers/system-of-measurement~metric/for-screw-size~m5/length~6-mm/od~10mm/) |
| 8 | 3mm allen key (M5) | 1 | For M5 button head screw | [McMaster-Carr](https://www.mcmaster.com/allen-keys/l-keys-9/system-of-measurement~metric/size~3-mm/) |
| 8 | M5 x 10mm screws | 20 | for mounting on the extrusions (need 11) | McMaster-Carr |
| 10 | M5 x 20mm screws | 12 | for carriage idlers (need 4), 1 for front idler | McMaster-Carr | |
| 13 | M5 x 35mm screws | 11 | for carriage v-wheels | McMaster-Carr |
| 1 | M3 x 10mm screws | 8 | for mounting the stepper motors | McMaster-Carr |
| 16 | SG90 Servo Motor | 1 | | [Amazon](https://www.amazon.com/Smraza-Helicopter-Airplane-Control-Arduino/dp/B07L2SF3R4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) |
| ? | Rubber Feet | 8 | For attachment to the bottom of the feet | [Amazon](https://www.amazon.com/Door-Bumpers，1-Bumpers-Furniture-Dampening/dp/B0BP8BNG7B/) |
| box  | 20mm x 20mm v slot extrusion | 2 | | [OpenBuilds](https://openbuildspartstore.com/v-slot-20x20-linear-rail/?sku=255-LP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) |
| box  | Nema 17 Stepper Motor | 2 | | [Amazon](https://www.amazon.com/STEPPERONLINE-Stepper-63-74oz-Connector-Extruder/dp/B07LCHHQ97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) |
| box  | 8mm wrench | 1 | for adjusting eccentric spacers and belt tensioner | Amazon |

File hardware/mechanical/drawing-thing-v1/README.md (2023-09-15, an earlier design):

# Parts for Drawing Thing (with 3D printed carriage)



## Model

The [full model can be found here](https://cad.onshape.com/documents/093c10251b077919c05ae92c/w/7b13786fba2aec43dcfab15d/e/5687b6fe35f0477aa77dedea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).

## BOM

| Part | Quantity | Notes | Source |
| --- | --- | --- | --- |
| flanged bearings (625) | 10 | | [amazon](https://www.amazon.com/uxcell-Bearing-5x16x5mm-Shielded-Bearings/dp/B07Z3DXF14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) |
| gt2 timing belt | 1 | | [amazon](https://www.amazon.com/Printing-Zeelo-Fiberglass-Rostock-Printers/dp/B08974S1CC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) |
| 5mm nuts | 30 | | [mcmaster](https://www.mcmaster.com/nuts/metric-medium-strength-steel-hex-nuts-class-8/thread-size~m5/) |
| stepper motors | 2 | | [amazon](https://www.amazon.com/STEPPERONLINE-Stepper-63-74oz-Connector-Extruder/dp/B07LCHHQ97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) |
| t-nuts | 20 | | [amazon](https://www.amazon.com/Fastener-Nickel-Plated-Sliding-Aluminum-Profile/dp/B086MKNYDS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) |
| v-wheels | 8 | | [amazon](https://www.amazon.com/V-Shape-Bearing-Accessories-Sliding-Printer/dp/B07NSHH9N4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) |
| 6mm eccentric nut | 4 | | [openbuilds](https://www.amazon.com/Befenybay-Hexagonal-Eccentric-Column-Printer/dp/B08LMQ8JFY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) |
| 1mm spacers 10mm od | 5 | | [openbuilds](https://openbuildspartstore.com/precision-shim-10x5x1mm/) |
| 6mm spacers 10mm od | 4 | | [mcmaster](https://www.mcmaster.com/spacers/system-of-measurement~metric/for-screw-size~m5/length~6-mm/od~10mm/) |
| 20mm x 20mm v slot extrusion | 2 | | [openbuilds](https://openbuildspartstore.com/v-slot-20x20-linear-rail/?sku=255-LP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) |
| stepper motor tooth pulley (12mm dia) | 2 | | [amazon](https://www.amazon.com/GT2-Creality-Ender-3-Printer-Stepper/dp/B088WB8D7W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) |
| 5mm x 20mm screws | 6 | carriage idlers (need 4) | button head in my design |
| 5mm x 35mm screws | 10 | v-wheels (need 8) | button head in my design |
| 5mm x 30mm screws | 2 | belt clamp | button head in my design |
| 5mm x 10mm screws | 20 | mounting on the alu extrusions (need 11) | button head in my design |
| 5mm x 13mm screws | 4 | 12mm could also work, for the feet | button head in my design |
| 2.5mm x 10mm screws | 4 | | button head in my design |
| 3.5mm x 10mm screws | 8 | | button head in my design |
| servo motor | 1 | | [amazon](https://www.amazon.com/Smraza-Helicopter-Airplane-Control-Arduino/dp/B07L2SF3R4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) |
| 8mm wrench | 1 | | [amazon](https://www.amazon.com/Crescent-8mm-Point-Combination-Wrench/dp/B095KWT4QZ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) |
| 5mm allen key | 1 | | [mcmaster](https://www.mcmaster.com/allen-keys/l-keys-9/system-of-measurement~metric/size~5-mm/) |
| 3.5 mm allen key | 1 | | [mcmaster](https://www.mcmaster.com/allen-keys/l-keys-9/system-of-measurement~metric/size~3-5-mm/) |

# Printed Parts

Printed parts can be found in [/stls](./stls).

The quantity of each part is listed in the name as such `name_x${QUANTITY}`.

# Pen Holder

The pen holder is not accounted for above. A [potential design can be found here](https://cad.onshape.com/documents/c1f5eeb5e941fbf9d7330a99/w/dd3d59e4690b0b43272af915/e/82ecaea7c0ef64149c49e771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).

Note that this design requires a 2.5mm x 25mm screw and 2.5mm nut

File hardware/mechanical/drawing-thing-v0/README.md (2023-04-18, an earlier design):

# Drawing Thing

We're in the early stages of developing our next "you ship, we ship", you make some digital art and we'll send you a drawing robot which can fabricate that art.

Drawing thing is designed to be the best introduction to digital fabrication. It's a small machine you can own, take apart, play with, and modify at any level of its design. You can change the control software, path planning, machine interface and more all from a friendly browser-based IDE (and all in JavaScript).



We're also pushing the state of the art with how hackable these machines can be by working with some researchers at MIT to create a new framework for modular machine control called [Modular Things](https://github.com/modular-things/modular-things).

You can learn more about Modular Things in the linked repo but the gist is that it allows to write "firmware" for embedded devices without ever having to actually re-flash those devices. Instead the firmware all runs in a high level host (like the browser) and each board runs a small networking program which allows you to access their dedicated functions (like a motor control board).



That's cool and all but what can you do with them? Well whatever you want really, a good place to start is the sorts of things you would build with an Arduino but Modular Things is more extensible and accommodating of adding things like multiple
coordinate motors. That's why we're focused on building a delightful (and affordable) drawing machine.

The leading design is strongly influenced by the [AxiDraw MiniKit 2](https://cdn.evilmadscientist.com/dl/ad/public/AxiDraw_MiniKit_v2.5b.pdf). But we've looked at quite a few:

- https://www.amazon.com/Educational-Robots-Toys-Preschool-Learning/dp/B07Z5B5HQH
- https://www.aliexpress.us/item/3256804588342853.html
- https://axidraw.com/
- https://www.media.mit.edu/projects/open-drawing-machine/overview/
- https://github.com/montoyamoraga/open-drawing-machine
- http://davepreiss.github.io/Portfolio/
- https://www.thingiverse.com/thing:3554
- https://www.thingiverse.com/thing:2349232
- https://www.youtube.com/watch?v=CW3tCkms7oM
- https://www.youtube.com/watch?v=XYqx5wg4oLU

## Stuff to Do

There is a lot to do. As previously stated the aim is to make a good quality and affordable drawing machine which is easily hackable by building it with modular things. The basis of many machines is a motion system so we plan to develop the drawing machines motion system in a fairly generic way. The pen tool could be easily swapped for some other sort of end effector. The interface will be created with web technologies in the same environment that the machine control is written and both of these will be modifiable to the user. In order for the machine to perform well we have to improve the path planning and motor control programs. Currently the Modular Things architecture requires one USB per an embedded device. It'd be nice with the devices could be networked to each other so we're also looking at creating a link layer that runs microcontroller to microcontroller.

## Getting Involved

If you want to follow along as we build the project out you can follow along on Slack in [development-of-things-and-stuff](https://app.slack.com/client/T0266FRGM/C04GCH8A91D/thread/C04GCH8A91D-1672275851.810779)

You can also get started working on generative design and pen plotting. [Drawingbots](https://drawingbots.net/) is a good resources. Specifically the [tool section](https://drawingbots.net/knowledge/tools) has a bunch of programs for making plottable patterns.

Here are some blogs about plotting which are worth checking out:

- https://revdancatt.com/
- https://penplotterartwork.com/
- https://greweb.me/
- https://targz.fr/
- https://larswander.com/
- https://www.v3ga.net/
- https://bylr.info/
- http://andymakes.com/#Plotter
- https://www.eyesofpanda.com/
- https://mattdesl.svbtle.com/pen-plotter-1
- https://muffinman.io/art/

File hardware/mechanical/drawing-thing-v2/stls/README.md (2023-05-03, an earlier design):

# Notes on 3D printing the parts

- [belt-clamp_x1.stl](./belt-clamp_x1.stl)
- [foot_x2.stl](./foot_x2.stl)
- [motor-bracket_x2.stl](./motor-bracket_x2.stl)
- [printed-rail_x1.stl](./printed-rail_x1.stl)
- [belt-clamp-cap_x2.stl](./belt-clamp-cap_x2.stl)
- [carriage_x1.stl](./carriage_x1.stl)
- [idler-front_x1.stl](./idler-front_x1.stl)
- [pen-holder_x1.stl](./pen-holder_x1.stl)

parts on Prusa MINI bed

_I've tried to print the parts for this machine with various printers/filaments/beds/settings, and have listed my takeaways below. This was just my experience, so perhaps yours could be different._

- I recommend printing with PLA. Print at 90% speed for the first layer, with flow set to 105%. Then switch back to default (100 speed, 95 flow) after first layer.
  - 20% infill has been recommended for mechanical parts, but the 15% is probably fine.
  - If you print with PETG, you may have better results printing at lower speeds.
- .2mm is a good layer height to have sufficient screw hole/nut trap tolerances.
- Add circular feet (2x layer height) to corners for better adhesion.

- Don't use the textured beds!!!!!!!!
- If you're in a time crunch, best to print in 2 different batches. I've found 1 full sheet of parts to not always be successful.
- Clean bed with isopropyl alcohol

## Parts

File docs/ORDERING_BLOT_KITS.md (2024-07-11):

# How to Order Blot kits

Blot kits are provided by [ISource-Asia](http://www.isource-asia.com/). Our main contact there is Sam Hu.
I'm (Leo McElroy) going to describe how to order a kit from a contract manufacturer using Sam as an example.

The relationship with Sam was built when I traveled to Shenzhen in January 2024 to find a supplier. 
It's helpful to have a relationship with your supplier in China as a lot of communication can happen informally.
Sam and I communicate through email and WeChat.

I met a few contract manufacturers (who were all very welcoming and friendly). 
I provided each of them with the [BOM](https://raw.githubusercontent.com/hackclub/blot/main/docs/BOM.toml) for the Blot and requested they pack and send me a sample kit.
Each of these kits cost around $100 - $200.
Sam was the most expedient and thorough in this task, in addition to ultimately offering a good price. 

Sam prefers to view the BOM as a table and to download it as a CSV (as is the case with most contract manufacturers I spoke to) so I wrote [this utility website](https://leomcelroy.com/toml-table-viewer/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) to provide that functionality. 
Take note that to view files like this on GitHub someone in China will need to make use of a VPN.

The important columns are

  - the part name
  - the quantity
  - an example source
    - Sam will find a supplier in China for must parts but you can specify if he needs to purchase from the provided source
    - for parts that Sam will make you can link the design files such as stls (for 3D prints) or Gerbers, boms, component placements (for circuits)
  - any additional notes

It's helpful to include images as well. 
For the Blot Sam 3D prints some parts and also fabricates a metal plate. 
For the plate we provide DXF and STEP files.

You can also specify how you would like your parts to be packed, such as creating a custom box or foam.
Sam might also have clarifying questions about the job such as
 
  - Is this supplier an appropiate subsitute for the example provided?
  - Would you rather this part be laser cut or machined?
  - How big would you like the shipping box to be?
  - etc.

After answering these questions the test package took around 1-2 weeks to arrive.

I evaluated the kit by building the Blot taking note of any changes that needed to be made.

Some examples of changes from our first order was I determined the T-nuts we used were too difficult to place so we swapped them for some spring loaded notes.
We also discovered that I had specified the wrong units for the belt length (which Sam caught!), the proper units could be inferred fortunately so the belt length was still acceptable. 

After okaying the kit we order them by requesting an invoice from Sam which is fulfilled by our payment office (thanks Mel!).

Sam can ship kits directly from China to Hack Clubbers or can ship kits to the warehouse in Vermont.

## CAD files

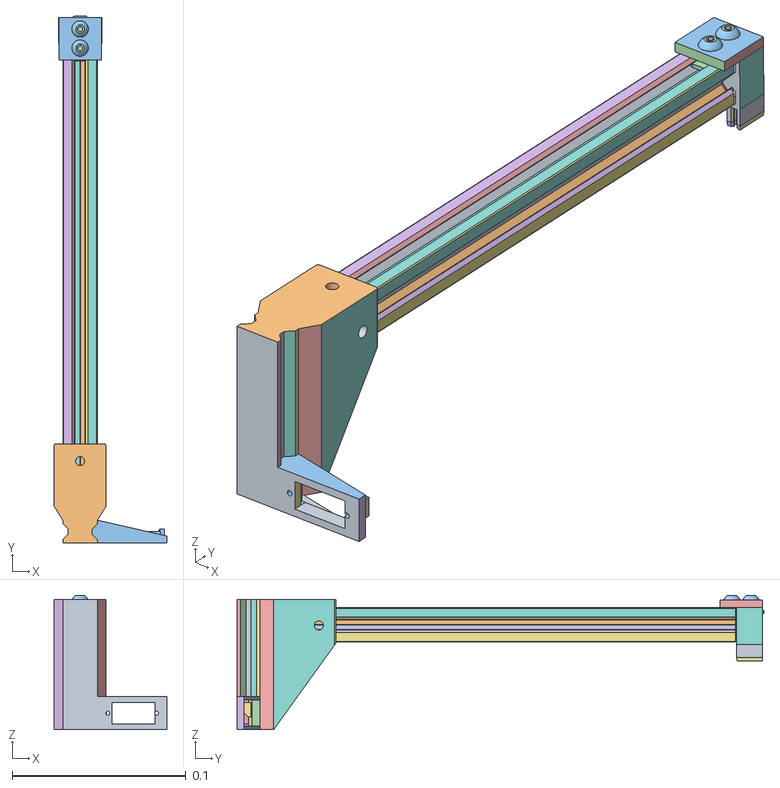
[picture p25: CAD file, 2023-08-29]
esbuild/public/model/arm.obj
0.065 x 0.304 x 0.0773

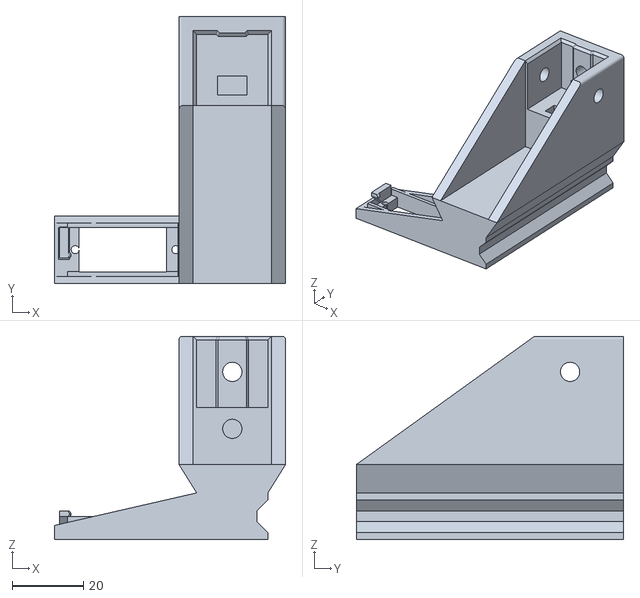
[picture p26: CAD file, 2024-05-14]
hardware/mechanical/blot-v6/1x_PrintedRail.stl
65.0 x 75.0 x 57.2

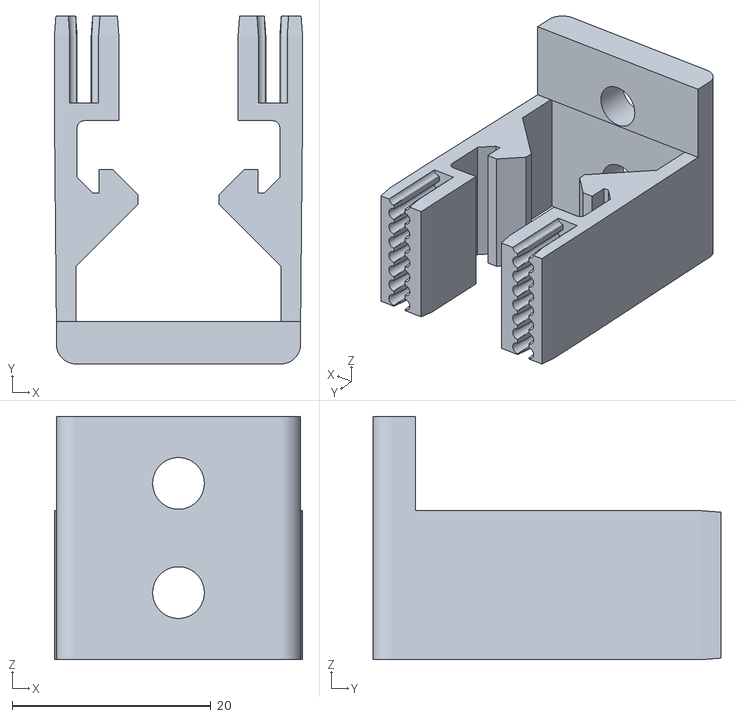
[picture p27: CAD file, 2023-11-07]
hardware/mechanical/drawing-thing-v5/1x_BeltClip.stl
25.0 x 35.1 x 24.5

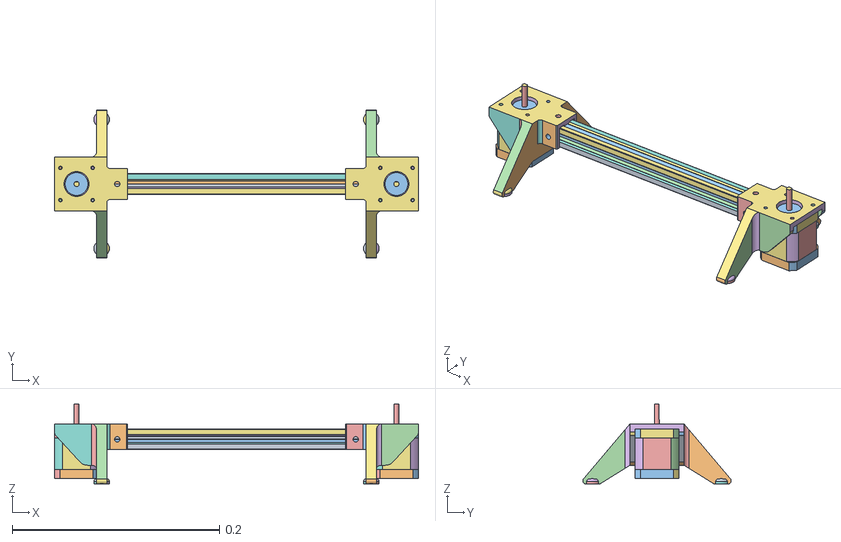
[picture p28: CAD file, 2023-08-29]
esbuild/public/model/feet.obj
0.351 x 0.143 x 0.077

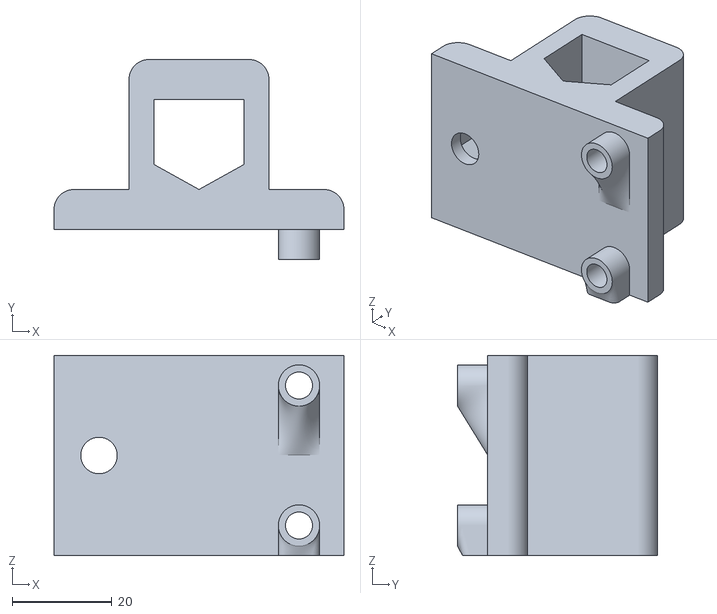
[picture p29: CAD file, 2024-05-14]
hardware/mechanical/blot-v6/1x_ToolHead.stl
58.0 x 40.0 x 40.0

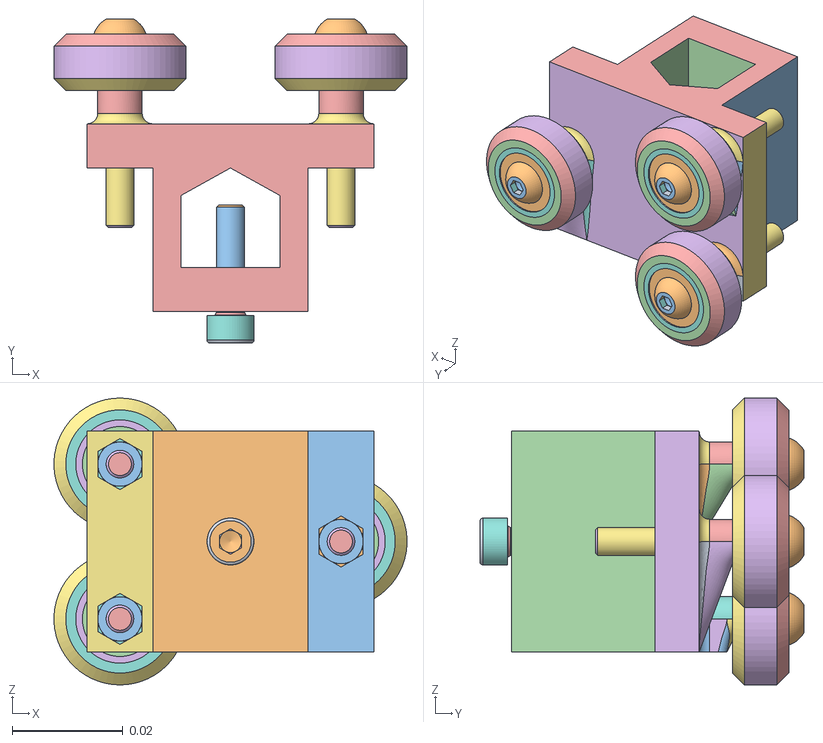
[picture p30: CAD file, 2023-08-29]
esbuild/public/model/penholder.obj
0.0639 x 0.0586 x 0.0519

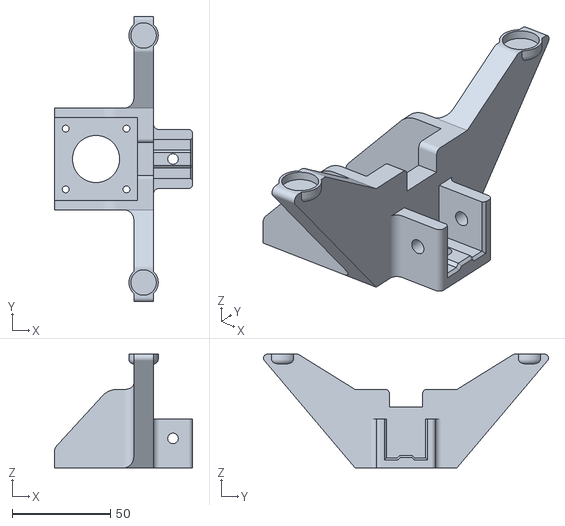
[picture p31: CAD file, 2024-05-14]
hardware/mechanical/blot-v6/2x_Legs.stl
70.5 x 145.4 x 58.0

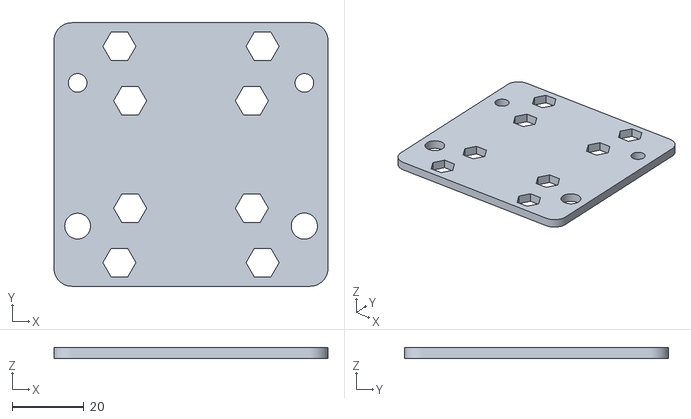
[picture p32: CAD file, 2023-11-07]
hardware/mechanical/drawing-thing-v5/1x_CarriagePlate.stl
76.5 x 73.6 x 3.17

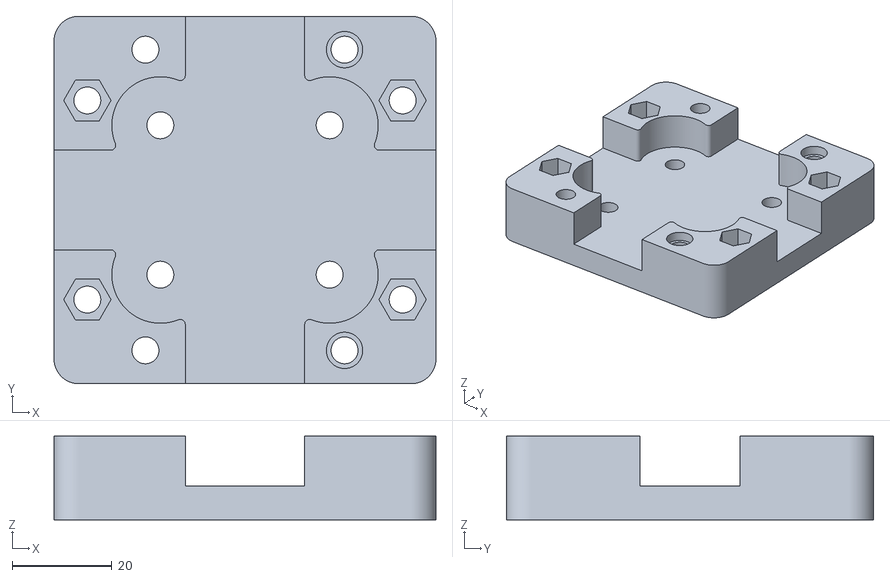
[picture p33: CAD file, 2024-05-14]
hardware/mechanical/blot-v6/1x_Carriage.stl
76.7 x 73.8 x 16.8

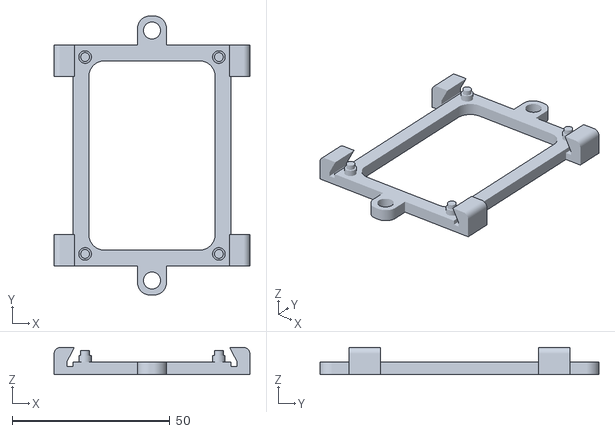
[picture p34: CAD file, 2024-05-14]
hardware/mechanical/blot-v6/1x_PcbMount.stl
62.0 x 88.4 x 8.60

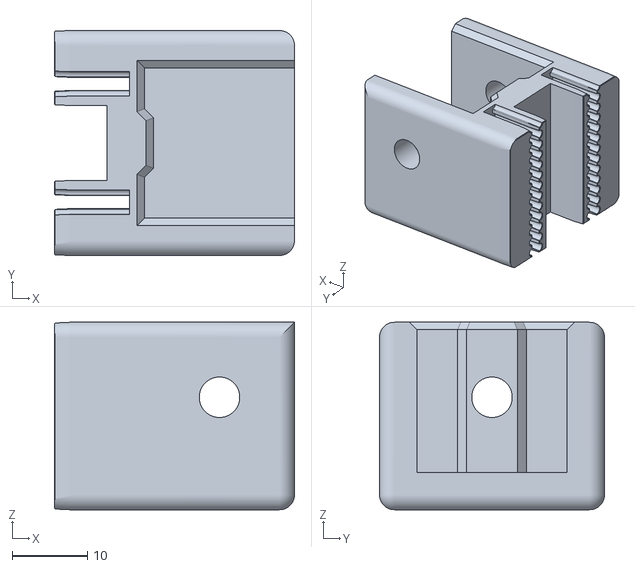
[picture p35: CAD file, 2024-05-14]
hardware/mechanical/blot-v6/1x_BeltClip.stl
32.0 x 30.0 x 25.0

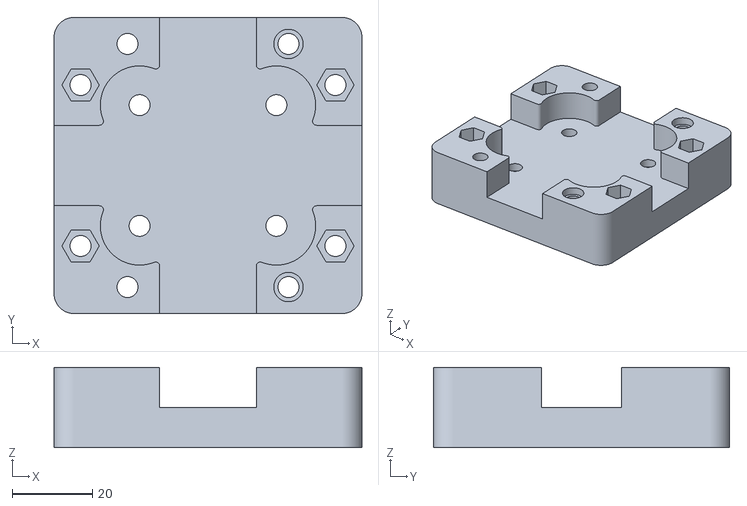
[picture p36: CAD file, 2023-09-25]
hardware/mechanical/drawing-thing-v5/1x_EccentricCarriage.stl
76.5 x 73.6 x 20.0

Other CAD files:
hardware/mechanical/drawing-thing-v5/1x_PrintedRail.stl
hardware/mechanical/drawing-thing-v5/1x_ReinforcedCarriage.stl
hardware/mechanical/blot-v6/1x_CarriagePlate.step
hardware/mechanical/drawing-thing-v5/2x_Legs.stl
hardware/mechanical/drawing-thing-v5/1x_PcbMount.stl
hardware/mechanical/drawing-thing-v5/1x_ToolHead.stl
hardware/mechanical/blot-v6/1x_CarriagePlate.dxf
hardware/mechanical/drawing-thing-v0/mechanical/Carriage - Carriage.dxf
hardware/mechanical/drawing-thing-v0/mechanical/Idler spacer - Idler spacer.stl
hardware/mechanical/drawing-thing-v0/mechanical/Pen holder - Pen holder.stl
hardware/mechanical/drawing-thing-v0/mechanical/Pen holder - Pen mount.stl
hardware/mechanical/drawing-thing-v0/mechanical/X rail - X axis motor bracket - left.dxf
hardware/mechanical/drawing-thing-v0/mechanical/X rail - X axis motor bracket - right.dxf
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

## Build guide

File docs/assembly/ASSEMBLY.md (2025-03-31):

# Blot Assembly

Congratulations! You've just received your Blot (or what is soon to be your Blot)! Get ready to jump into machine building. Don't worry we'll walk through everything in detail.

If you'd like to [watch a short video (6 minutes) of building a Blot you can click here](https://www.youtube.com/watch?v=7N-Nu6_oo4I).

It takes me about 30 minutes in real time to assemble a Blot but I have lots of experience (and designed the machine). Don't be discouraged if it takes a few hours (or more) there is a lot to learn along the way.

Here are all the parts that come with your Blot. The source of truth for the Blot components is the [BOM (Bill of Materials) available here](../BOM.toml).

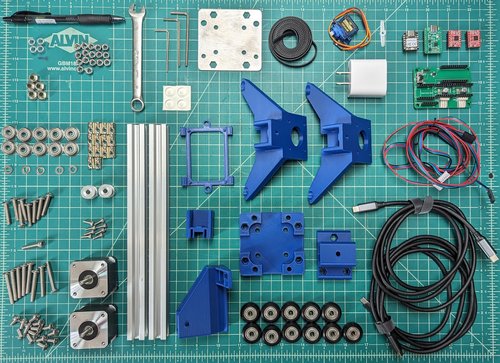
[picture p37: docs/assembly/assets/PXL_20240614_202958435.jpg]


| Quantity | Name | Image |
| --- | --- | --- |
| 1 | 3mm allen key | Screenshot 2024-07-10 at 2.00.28 PM.png |
| 1 | 2.5mm allen key | Screenshot 2024-07-10 at 2.01.33 PM.png |
| 1 | 2mm allen key | Screenshot 2024-07-10 at 2.02.03 PM.png |
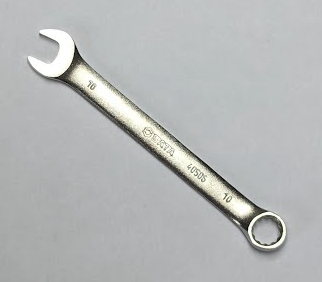
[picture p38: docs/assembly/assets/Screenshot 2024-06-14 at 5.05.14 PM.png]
| 1 | 10mm wrench |  |
| 8 | M5x35 Button Cap Screw |  |
| 8 | M5x25 Button Cap Screw |  |
| 17 | M5 Nut |  |
| 14 | M5 T-nut |  |
| 1 | M5x20, knurled cylinder head |  |
| 2 | Timing Belt Pulley |  |
| 14 | M5x10 Button Cap Screw |  |
| 4 | Rubber Feet (less than .5in diameter) |  |
| 8 | M3x10 Button Cap Screw |  |
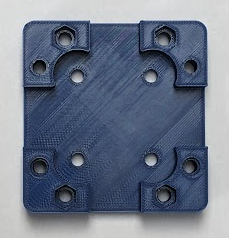
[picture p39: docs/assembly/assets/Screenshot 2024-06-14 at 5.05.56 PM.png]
| 1 | Carriage |  |
| 5 | Aluminum Spacer (1mm tall x 10mm OD)  |  |
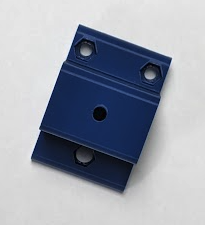
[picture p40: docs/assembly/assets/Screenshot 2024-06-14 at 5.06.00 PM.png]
| 1 | Tool Head |  |
| 5 | Eccentric Spacer (6mm tall) |  |
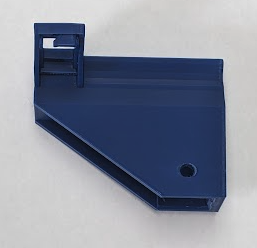
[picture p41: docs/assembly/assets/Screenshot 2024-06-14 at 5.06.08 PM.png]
| 1 | Printed Rail |  |
| 4 | Aluminum Spacer (6mm tall x 8mm OD) |  |
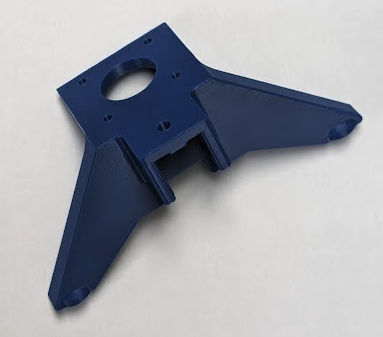
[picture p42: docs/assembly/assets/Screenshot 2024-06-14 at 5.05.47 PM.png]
| 2 | Motor Leg |  |
| 11 | 625zz V-Wheel |  |
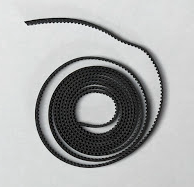
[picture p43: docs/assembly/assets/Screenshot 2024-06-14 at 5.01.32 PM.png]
| 1 | 125cm long GT2 Timing Belt |  |
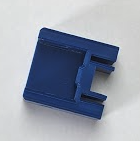
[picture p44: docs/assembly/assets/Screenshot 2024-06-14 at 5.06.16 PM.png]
| 1 | Belt Clip |  |
| 10 | Flanged bearing (5x16x5mm) |  |
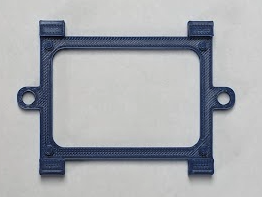
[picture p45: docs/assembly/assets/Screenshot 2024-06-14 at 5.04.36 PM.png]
| 1 | PCB Mount |  |
| 2 | 20mm x 20mm Aluminum Extrusion |  |
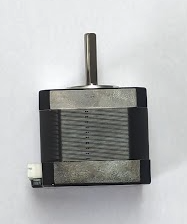
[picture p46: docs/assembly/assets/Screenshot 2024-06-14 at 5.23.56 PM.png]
| 2 | Stepper Motor (42mm x 42mm) |  |
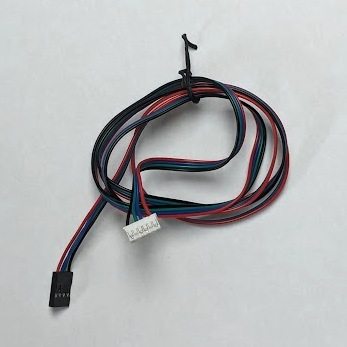
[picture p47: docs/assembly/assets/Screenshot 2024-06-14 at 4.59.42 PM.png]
| 2 | 20mm Stepper Motor Cables |  |
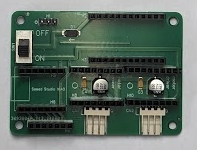
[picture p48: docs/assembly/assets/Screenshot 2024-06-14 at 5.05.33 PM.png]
| 1 | PCB - Control Board |  |
| 1 | PCB - Power Board |  |
| 1 | Xiao RP2040 |  |
| 2 | a4988 Stepper Motor Driver |  |
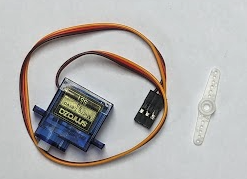
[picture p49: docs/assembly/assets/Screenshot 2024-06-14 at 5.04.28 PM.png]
| 1 | Servo + Arm (25mm cable) |  |
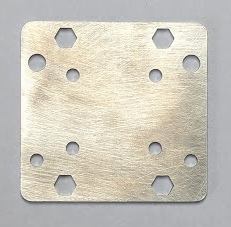
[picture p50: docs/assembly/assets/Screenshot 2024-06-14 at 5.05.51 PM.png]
| 1 | Carriage Plate |  |
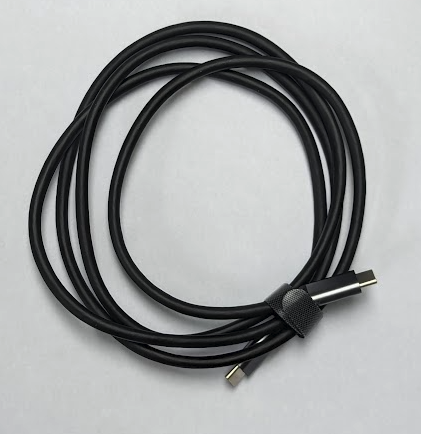
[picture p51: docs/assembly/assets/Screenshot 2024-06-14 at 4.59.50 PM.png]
| 2 | USB-C to USB-C Cable |  |
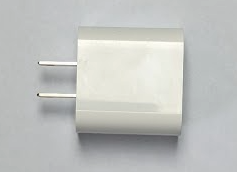
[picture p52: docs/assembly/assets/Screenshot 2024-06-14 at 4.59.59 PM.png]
| 1 | USB-C Charger (Brick) |  |
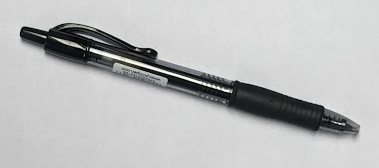
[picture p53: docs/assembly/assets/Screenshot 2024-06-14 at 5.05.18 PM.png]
| 1 | Pilot G-2 Roller Pen |  |

<!-- 
- __1 x__ 3mm allen key
- __1 x__ 2.5mm allen key
- __1 x__ 2mm allen key
- __1 x__ 10mm wrench
- __8 x__ M5x35 Button Cap Screw
- __8 x__ M5x25 Button Cap Screw
- __17 x__ M5 Nut
- __14 x__ M5 T-nut
- __1 x__ M5x20, knurled cylinder head
- __2 x__ Timing Belt Pulley
- __14 x__ M5x10 Button Cap Screw
- __4 x__ less than .5in diameter Rubber Feet
- __8 x__ M3x10 Button Cap Screw
- __1 x__ Carriage
- __5 x__ 1mm tall x 10mm OD x M5 inner Alumninum Spacer
- __1 x__ Tool Head
- __5 x__ 6mm tall x M5 inner Eccentric Spacer
- __1 x__ Printed Rail
- __4 x__ 6mm tall x 8mm OD x M5 inner Alumnium Spacer
- __2 x__ Motor Leg
- __11 x__ 625zz V-Wheel
- __1 x__ 125cm long GT2 Timing Belt
- __1 x__ Belt Clip
- __10 x__ 5x16x5mm flanged bearing
- __1 x__ PCB Mount
- __2 x__ 20mm x 20mm (face) x 250mm (tall) Aluminum Extrusion
- __2 x__ 42mm x 42mm (face) x 38mm (tall) Stepper Motor
- __2 x__ 20mm Stepper motor cables
- __1 x__ PCB - control board
- __1 x__ PCB - power board
- __1 x__ Xiao RP2040
- __2 x__ a4988 stepper motor driver
- __1 x__ Servo (25mm cable) + arm
- __1 x__ Carriage Plate
- __2 x__ usb-c to usb-c cable
- __1 x__ usb-c charger (brick)
- __1 x__ Pilot G-2 roller pen
 -->

### The carriage

The first part of the Blot we will assemble looks like this

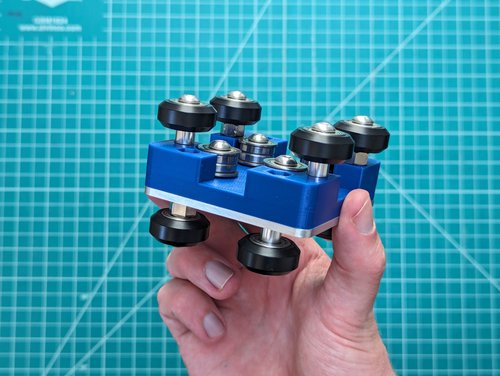
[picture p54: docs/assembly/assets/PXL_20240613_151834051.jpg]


It uses these parts:

- __4 x__ M5x25 Button Cap Screw
- __8 x__ M5x35 Button Cap Screw
- __8 x__ 625zz V-Wheel
- __8 x__ 5x16x5mm flanged bearing
- __4 x__ 6mm tall x 8mm OD x M5 inner Alumnium Spacer
- __12 x__ M5 Nut
- __4 x__ 6mm tall x M5 inner Eccentric Spacer
- __4 x__ 1mm tall x 10mm OD x M5 inner Alumninum Spacer
- __1 x__ Carriage
- __1 x__ Carriage Plate

You'll need these tools:

- __1 x__ 3mm allen key

Align the metal plate with the carriage. It will only align one way.

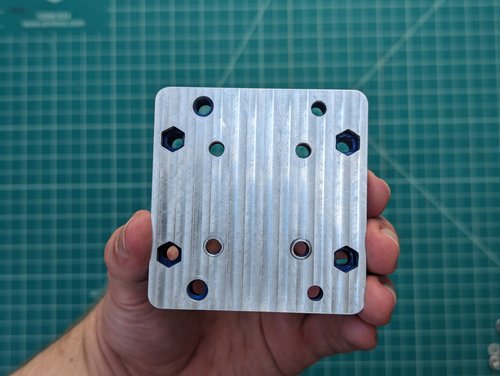
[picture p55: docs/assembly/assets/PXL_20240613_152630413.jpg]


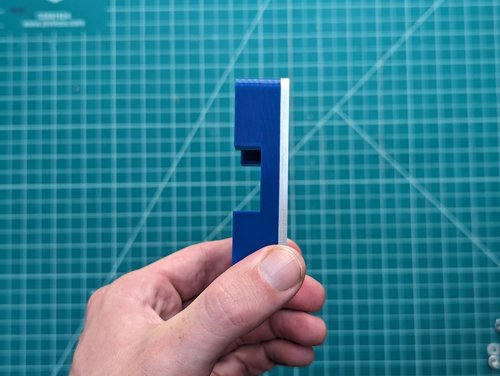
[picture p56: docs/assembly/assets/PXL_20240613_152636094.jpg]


Well start by putting the idlers on. Begin by stacking 2 flanged bearings and a spacer on a 25mm screw.

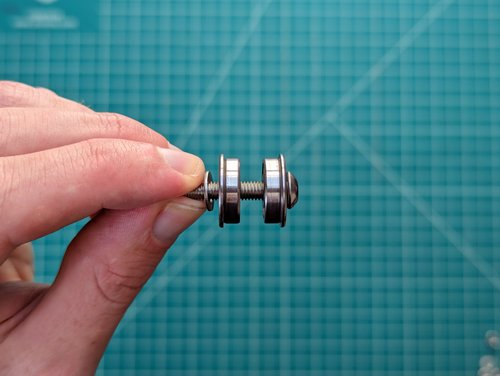
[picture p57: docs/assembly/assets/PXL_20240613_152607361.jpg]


Place that screw through the metal plate and use a nut to secure the assembly.

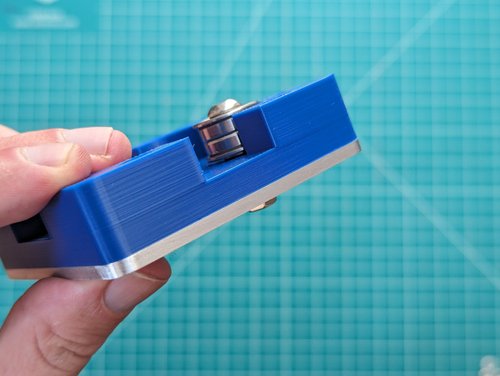
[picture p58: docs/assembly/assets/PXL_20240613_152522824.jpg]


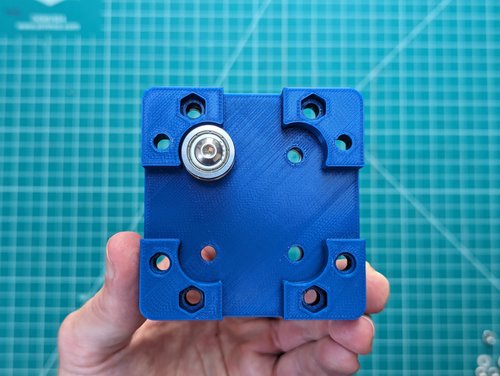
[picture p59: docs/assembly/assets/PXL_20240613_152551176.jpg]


Repeat three more times.

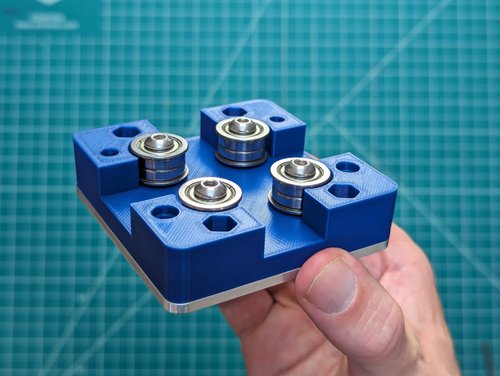
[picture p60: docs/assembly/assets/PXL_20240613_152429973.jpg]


Now let's attach the 8 v-wheels.

You'll notice that some of the holes are a bit larger. We'll place eccentric nuts in them which will allow us to tune the machine.

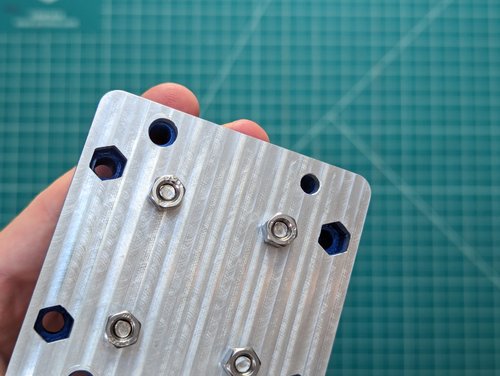
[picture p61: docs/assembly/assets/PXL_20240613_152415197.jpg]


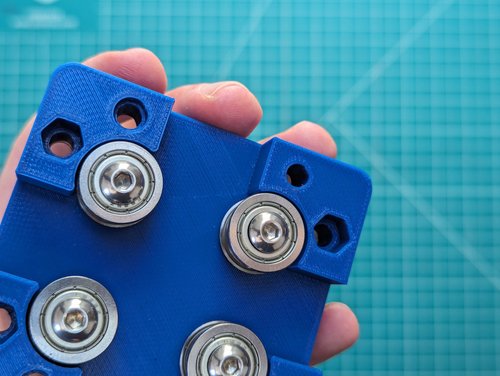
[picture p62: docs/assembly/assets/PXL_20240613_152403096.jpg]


Take a 35mm screw and an eccentric nut. 

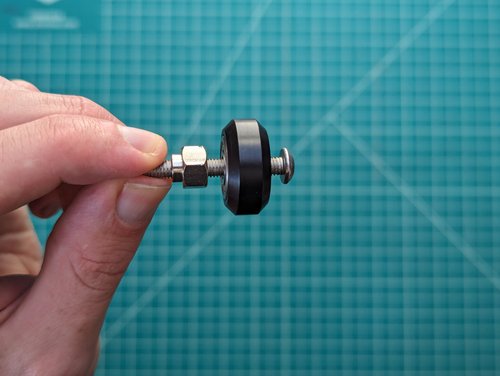
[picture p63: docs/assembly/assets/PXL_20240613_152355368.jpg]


If the washer inside the bearing of the v-wheel is misaligned you can re-align it with an allen key.

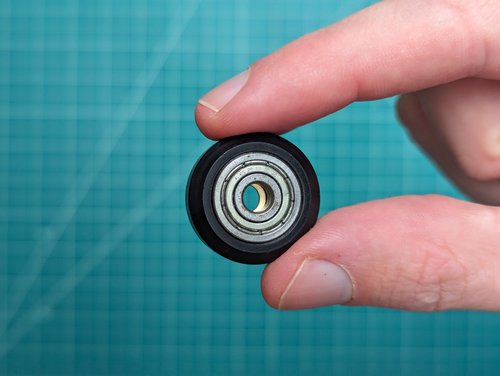
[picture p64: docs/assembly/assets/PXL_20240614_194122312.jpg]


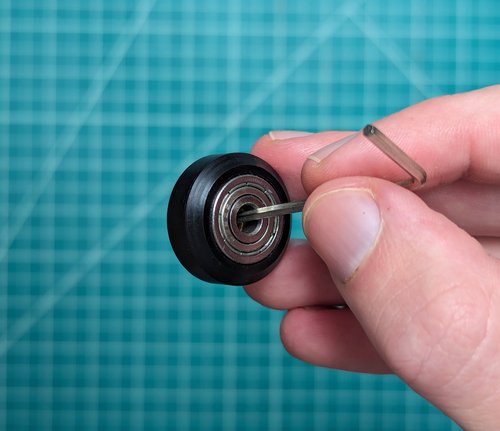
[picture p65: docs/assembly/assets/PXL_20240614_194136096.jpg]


Slip it into one of the larger holes and place a nut in the trap on the alternate side. Then tighten the screw.

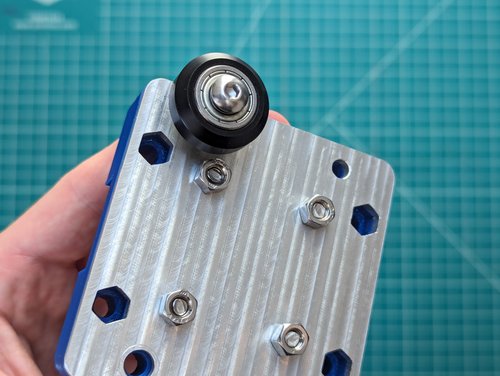
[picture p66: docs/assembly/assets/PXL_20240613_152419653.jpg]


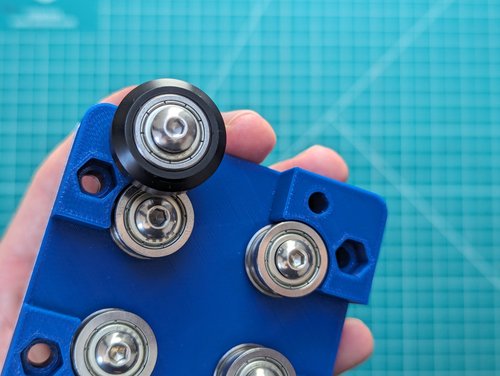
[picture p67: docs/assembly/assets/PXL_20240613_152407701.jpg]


Repeat for the other eccentric nuts.

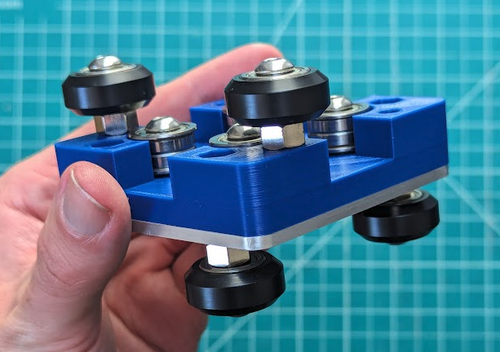
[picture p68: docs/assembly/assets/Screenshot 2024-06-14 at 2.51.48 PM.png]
Screenshot 2024-06-14 at 2.51.48 PM.png


Now let's do the same thing for the non-adjustable v-wheels.

Take a 35mm screw and a 6mm spacer with a v-wheel and assemble like below.

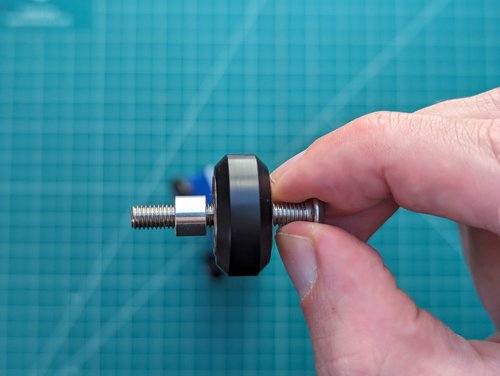
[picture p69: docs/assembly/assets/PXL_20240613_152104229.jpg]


Attach those to the assembly as we did with the other v-wheels. With those attached our assembly is complete.

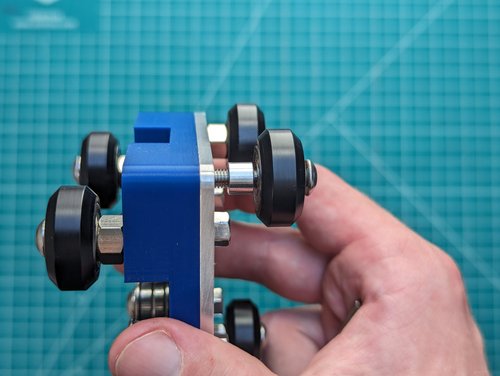
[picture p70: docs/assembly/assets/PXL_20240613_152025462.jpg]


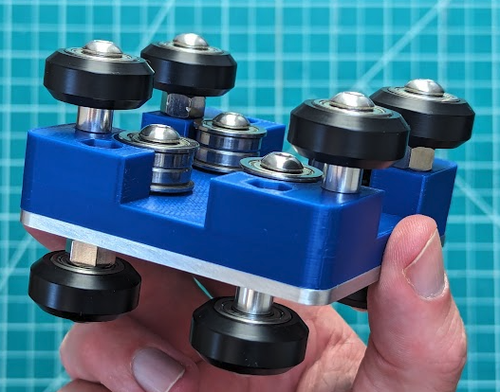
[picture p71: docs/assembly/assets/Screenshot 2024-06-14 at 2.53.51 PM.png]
Screenshot 2024-06-14 at 2.53.51 PM.png


### Leg Assembly

Let's put together the legs of the machine.

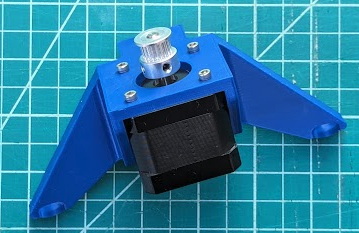
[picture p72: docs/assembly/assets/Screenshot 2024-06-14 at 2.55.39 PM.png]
Screenshot 2024-06-14 at 2.55.39 PM.png


You'll need these parts:

- __2 x__ Timing Belt Pulley
- __4 x__ less than .5in diameter Rubber Feet
- __8 x__ M3x10 Button Cap Screw
- __2 x__ Motor Leg
- __2 x__ 42mm x 42mm (face) x 38mm (tall) Stepper Motors

And these tools:

- __1 x__ 2.5mm allen key
- __1 x__ 2mm allen key

We'll start by placing the timing belt pulley on to the shaft of the stepper motor. The top of the pulley should be flush with the top of the shaft.

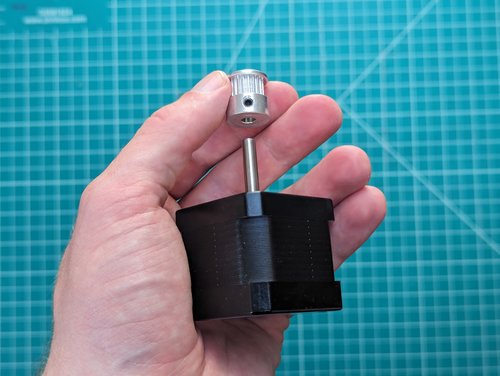
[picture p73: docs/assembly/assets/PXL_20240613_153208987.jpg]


Tighten the set screw with the 2mm allen key.

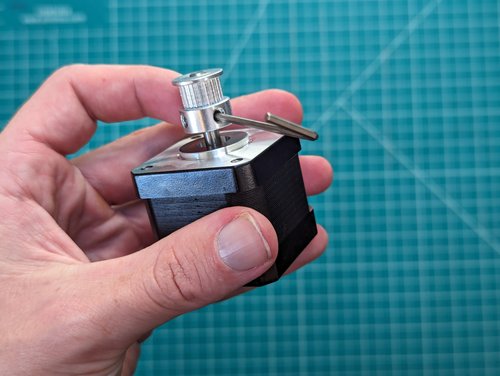
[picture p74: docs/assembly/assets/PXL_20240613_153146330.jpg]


Place the stepper motor into the leg with the cable port fitting into the cutout in the leg.

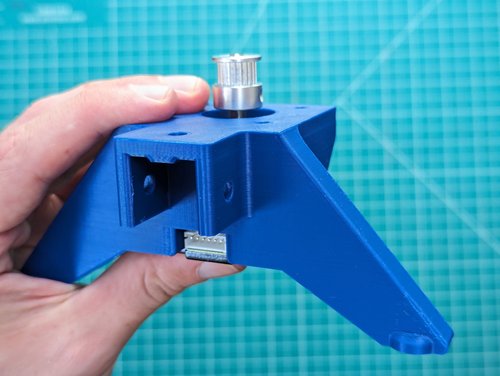
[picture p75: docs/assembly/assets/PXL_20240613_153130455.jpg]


Secure the motor in place with the M3x10mm screws.

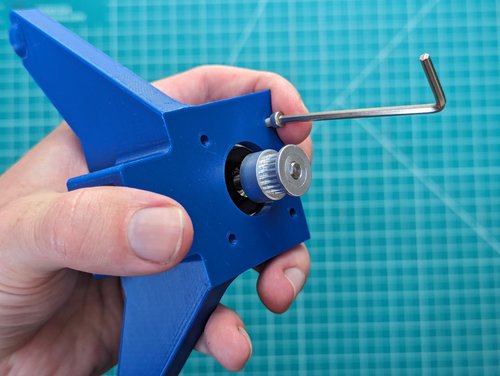
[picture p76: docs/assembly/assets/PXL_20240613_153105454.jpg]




Place the rubber feet on the leg.

Screenshot 2024-06-14 at 4.55.06 PM.png



Repeat this for the other leg.

We're done!

### Pen Rail



To put together the pen rail you'll need:

- __1 x__ 3mm allen key
- __1 x__ M5x25 Button Cap Screw
- __1 x__ M5 Nut
- __1 x__ 1mm tall x 10mm OD x M5 inner Alumninum Spacer
- __1 x__ Printed Rail
- __2 x__ 5x16x5mm flanged bearing
- __1 x__ Servo (25mm cable) + arm

You'll need these tools:

- __1 x__ 3mm allen key

First put together another idler stack on a M5x25 screw.



Place a nut into the cutout on the printer rail and secure the idler to it.



### Pen Holder

Let's make the pen holder.



You'll need these parts:

- __3 x__ M5x25 Button Cap Screw
- __4 x__ M5 Nut
- __1 x__ M5x20, knurled cylinder head
- __1 x__ Tool Head
- __1 x__ 6mm tall x M5 inner Eccentric Spacer
- __3 x__ 625zz V-Wheel

You'll need these tools:

- __1 x__ 3mm allen key

Let's add the eccentric wheel first. Make a stack with the M5x25 screw like so



Attach it to the pen holder by slipping it through the printed part and securing a nut on the back.

Screenshot 2024-06-14 at 4.54.00 PM.png

Attach the two fixed wheels with the remaining 2 M5x25 screws. 

Screenshot 2024-06-14 at 4.54.30 PM.png

Slip the nut into the trap on front portion of the pen holder and secure it with the knurled screw. We'll use this screw to clamp tools we place in the holder.





### Putting the machine together

Now we're ready for the machine to really come together. It will look like this.



You'll need these parts in addition to the sub-assemblies you just put together.

- **14 x** M5 T-nut
- **14 x** M5x10 Button Cap Screw
- **1 x** Belt Clip
- **1 x** PCB Mount
- **2 x** 20mm x 20mm (face) x 250mm (tall) Aluminum Extrusion

Additionally, you'll need these tools:

- **1 x** 3mm allen key
- **1 x** 10mm wrench

Begin by taking a piece of aluminum extrusion and inserting the t-nuts. I prefer to place the hole closer to the center of the bar. This will make the t-nut not visible when the part is mounted to it.

Screenshot 2024-06-14 at 3.06.42 PM.png

Place one of the legs on top of the end of the bar.

Screenshot 2024-06-14 at 3.12.42 PM.png

Secure it in place with M5x10 screws.

Screenshot 2024-06-14 at 3.13.31 PM.png

If the T-nut is misaligned, you can center it with the allen key.

Screenshot 2024-06-14 at 4.57.55 PM.png

Adjust the eccentric nuts on the carriage to make it loosely fit on the rail.

Screenshot 2024-06-14 at 3.15.43 PM.png

Screenshot 2024-06-14 at 3.15.35 PM.png

Now slide the carriage onto the rail. Notice how the aluminum plate faces the aluminum extrusion.



You can now adjust the nuts to make the wheels ride snugly. Don't make it too tight, just tight enough that the carriage doesn't rock back and fourth.

Screenshot 2024-06-14 at 3.18.43 PM.png

Now add the other leg.

Screenshot 2024-06-14 at 3.20.36 PM.png

Time to add the top rail.

Attach the printed pen rail to one end of the other extrusion.

Screenshot 2024-06-14 at 4.57.06 PM.png

Screenshot 2024-06-14 at 3.21.55 PM.png

Place that exstrusion on the carriage, adjusting the v-wheels as shown above.

Screenshot 2024-06-14 at 3.22.09 PM.png

Attach the belt clip to the end of the carriage facing down and secure it in place with M5x10 screws and t-nuts.

Screenshot 2024-06-14 at 3.22.24 PM.png



Flip the machine upside down and use the remaining two T-nuts to attach the motor mount.





### Threading the Timing Belt

For this step, you'll need the assembly you just made and the timing belt.

- **1 x** 125cm long GT2 Timing Belt



To start, turn the machine upside down.

We'll place one loop of the belt in the endcap.







Thread the belt through the carriage so a loop sticks out the other side.



Place that loop over the idler.



I now flip the Blot right-side up and use an allen key to push one loop of belt out.



Run that loop over one of the stepper motor pulleys.



Now repeat for the other side.



Pull the belt tight around the stepper motor pulley.



Flip the Blot over and fold the belt to push into the other side of the belt clamp. Make sure to pull the belt tight.





Congratulations! You've finished putting together the mechanical parts of the Blot.



### Wiring

- **1 x** PCB - control board
- **1 x** Xiao RP2040
- **2 x** a4988 stepper motor driver
- **1 x** Servo (25mm cable) + arm
- **2 x** 20mm Stepper motor cables

Insert the servo into the press fit holder. I place it so the arm is closer to the rail.



You first slip one side underneath the ledge.



Then push down on the outside edge.



Add the lever arm.



And we're done with this part.

Now assemble the control board



Make sure the potentiometers (round metal things) on the red boards are on the side with the black control board (Xiao).

Screenshot 2024-06-14 at 5.05.22 PM.png

Insert the control board into the machine.







Plug in all the wires.

First, plug in the servo motor wires. That's the brown, red, yellow wires. 

It's **very important** that the brown wire be on the side with the little circle. That means the metal pins will be on the inner side of the board (not facing the outer edge).





Now plug in the stepper motor wires.







The wires are a bit too long.



I like to address this by wrapping them around the feet of the Blot when they are plugged in. This can be down in different ways.



The machine will work with any configuration of how the stepper motor pins are plugged in. Depending on how your stepper motors are plugged in the drawing may be mirrored. You can correct this by changing whether the motors are plugged in with the metal pins showing face up or hidden face down. The correct orientation may be some combination of the two. I'll note this again when we cover setting the machine origin.

Note stepper motors plugged in with the metal pins up.



Note stepper motors plugged in with the metal pins down.

Screenshot 2024-07-10 at 1.29.09 PM.png

Adjust the eccentric nut on the pen carriage so it rides smoothly. Not too tight. Just tight enough not to jiggle.



Ready to run.

### Running Your Blot

Now it's time to run your Blot. 

[Check out a quick video demonstrating how to run a Blot here.](https://youtu.be/qDP5CNjFHJE)

To run your Blot you'll have to:

- Flash firmware to your Blot
- Connecting
  - Power your Blot.
  - Connect it to the web editor.
- Home your machine (set the origin).
- Fixture paper to draw on.
- Set the lever on the servo.
- Set the pen height for drawing.

__Flashing Firmware__

The first step to running your Blot is to flash the Blot firmware to the Xiao.

[You can download the firmware here.](https://github.com/hackclub/blot/raw/main/hardware/motor-control-board/firmware/uf2/firmware.ino.uf2)

First hold down the boot button (right button with a small `B` next to it) on your Xiao and then plug it into your computer while still holding the button.



It should appear as a drive, at which point you can release the button. If it doesn't appear, try again until it appears.

Next drop the firmware `.uf2` file onto drive.

Now the firmware is flashed.

__Connecting__

To power the Blot plug it into the USB-C brick that comes with your machine. Any USB-C brick that can deliver at least 20W should work. The Blot expects 9V 1A.

Flip the power switch on the board to turn the Blot on.



Connect your Blot to the web editor by plugging the Xiao in over USB.



Connect to your Blot by hovering over `Machine control` and selecting `Connect to machine`

Screenshot 2024-07-10 at 5.05.53 PM.png

If this is the first time you've connected with this Blot you'll get a pop-up to authorize the web serial connection. Select the item that says "Xiao".

__Homing__

To home your Blot.

Turn off the motors.

Screenshot 2024-07-10 at 4.58.46 PM.png

Manually move the Blot to the center position.



Turn on the motors.

Screenshot 2024-07-10 at 4.59.27 PM.png

Click `Move towards origin`. Note which corner the Blot moves towards.

Screenshot 2024-07-10 at 5.00.16 PM.png

Turn off the motors.

Screenshot 2024-07-10 at 4.58.46 PM.png

Manually move your Blot all the way to the corner it moved towards.



Click `Set Origin`.

Screenshot 2024-07-10 at 5.01.21 PM.png

Turn on the motors.

Screenshot 2024-07-10 at 4.59.27 PM.png

Depending on how your stepper motors are plugged in the drawing may be mirrored. You can correct this by changing whether the motors are plugged in with the metal pins showing face up or hidden face down. The correct orientation may be some combination of the two.

__Fixturing Paper__

Secure a piece of paper to draw on. I generally tape (or magnet down) the other side of the paper too.



__Setting Lever__

The servo lever lifts the pen. To set the servo lever range properly.

Remove the lever arm from the servo.



Set the pen to the up position in the editor.

Screenshot 2024-07-10 at 5.01.58 PM.png

Place the lever arm back on in the up position.

__Setting the Pen Height__

Loosen the set screw on the pen.

Move the pen to be just above the paper in the up position.

It should look like this when you are done.



__Draw!__

Pull up the art piece you want to draw in the code editor.

Hit `Run` to render the piece in the editor.

Screenshot 2024-07-10 at 5.07.56 PM.png

Then hover over `Machine control` and select `Run machine`.

Screenshot 2024-07-10 at 5.08.35 PM.png

Note that you must keep this tab active, or the communication speed (and your machine) will slow down. If you want to do something else on the computer just move the tab to a new window.

Watch Blot turn the code into a real thing.

Screenshot 2024-07-11 at 2.01.34 PM.png

For best results, I like to use a whiteboard ([which I bought for $10 at Target](https://www.amazon.com/Brand-Frameless-Magnetic-Dry-Erase-Board/dp/B0845T7JLC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)) with magnets to provide a flat surface and hold down paper.



### Send us a Postcard

We're building a Blot art wall back at HQ. After you build your machine pick up a local postcard and use Blot to draw your art on the back.

I picked up this cool vintage postcard from the antique store next door to Hack Club HQ. It shows a Vermont lake.



Here it is with my art piece drawn on the back. Ready to send to HQ.

Make sure you sign it too!



Hack Club HQ address is

```
Hack Club
15 Falls Rd 
Shelburne, VT 05482
USA
```

### Debugging Common Issues

Your Blot can draw quite precisely, poor performance is often due to:

- Bad wheel spacing on the carriage or pen holder.
  
  - To address this use the wrench to turn the eccentric nuts. The rails or pen holder should not move other than the direction they are intended to slide in when you shake them. The wheels should be just tight enough to hold things in place.

- Bad pen height.
  
  - If your drawing has irregular pen strokes your pen may not be low enough or your surface may be uneven.

- Machine improperly homed.

  - Ensure that your blot is all the way in the correct corner when you press set origin. Then ensure your blot starts in that same corner when you run your project.

- Paper sliding.
  
  - To secure the paper you can place one end beneath the Blot.
  
  - You can use tape to secure the other side.
  
  - You can also purchase a small whiteboard with magnets. I've found this to be the most reliable technique.

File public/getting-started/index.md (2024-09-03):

---
title: Getting started with Blot
---

Blot is a way to build interactive art through code. The instructions you write in this editor can generate art on screen, but they can also control the Blot drawing machine!

This guide will introduce you to some of the main tools in the toolkit, and help you make your first artwork. As you work through it, you will see **text in bold, with suggested challenges**, but you should also feel free to just tinker with your own ideas. Along the way, we'll also use the example of drawing a feather, just to demonstrate what can be achieved with each set of tools.

If you are a complete beginner to JavaScript, we recommend watching [this short introduction to programming](https://youtu.be/3KAan1PzmxA).



### Drawing lines

To use Blot, you will write code to define lines, then call the `drawLines` function. When you click "run", these lines will be drawn either on screen or in the real world, using a connected Blot machine.

You can use plain JavaScript, or any of the "toolkit" functions provided. Your job is just to turn your ideas into lines: Blot will do the rest!

The simplest way to draw a line is by specifying its coordinates. Here is one way to draw a line from the bottom left to the top right:

```js
const width = 125;
const height = 125;

setDocDimensions(width, height);

drawLines([
    [[0, 0], [width, height]]
])
```

Type in the code from above, run it, and make sure that you see something like this:



**Next, try changing it. Can you draw a line from top left to bottom right, instead? Could you draw a square?**

By the way, we are setting the document dimensions to 125x125 because that is a sensible limit, in millimeters, when using a physical Blot machine. 0,0 is located in the bottom left. See [setDocDimensions](/docs#setDocDimensions) for more info.

You can generate lines in a number of different ways, including plain JavaScript. One way to draw a square with sides of length `s` could be:

```js
const s = 50

drawLines([
    [[0, 0], [0, s]],
    [[0, s], [s, s]],
    [[s, s], [s, 0]],
    [[s, 0], [0, 0]]
])
```

Here we are calling `drawLines` with a JavaScript array of four lines, which are themselves just pairs of points. You may notice that it's pretty repetitive: we're specifying each point as both the start of one line and end of the other. Luckily we can call `drawLines` with a "polyline", which is just a line several connected points. You can think of these as locations that the Blot drawing machine will move, one after the other, with the pen down. As a polyline, we could draw our square like this:

```js
const s = 50;

drawLines([
    [[0, 0], [0, s], [s, s], [s, 0], [0, 0]]
])
```

**Notice that our polyline has 5 points. What do you think would have been drawn if we had forgotten to include the final one?**

It turns out that a lot of our drawings will have connected lines, so we'll be using polylines a lot. As we get more creative, we'll also want better ways of generating our generating these polylines!

### Turtle drawing

Let's say you wanted to draw a more interesting shape, like a triangle or a pentagon or a hamster. Finding the coordinates of the triangle might not be too hard, but the others are starting to feel tricky!

Sometimes, it's easier to draw shapes like this by imagining that our pen is like a little turtle on the page, that can turn a certain amount left and right, walk forward, and jump around. If it's easier to think about how your pen moves than _where your pen moves to_, you may want to use a turtle.

Here is how you might draw a triangle, for instance, remembering that a turtle would need to rotate itself 120 degrees each time to point in the right direction.

```js
const t = new bt.Turtle()
const size = 100

t.forward(size)
t.left(120)
t.forward(size)
t.left(120)
t.forward(size)

drawLines(t.lines())
```

**Copy this code into the editor and confirm that it draws a triangle. Can you draw a pentagon instead?**

<details>
<summary>See answer</summary>
One way to draw a pentagon might be to write code much like the above, but turn 72 degrees instead of 120, and go forward 5 times instead of 3. You could also start to see that squares, triangles and pentagons all have similar instructions, and decide to make that into a JavaScript function that can draw any regular polygon:

```js
const shape = (n, size) => {
  const t = new bt.Turtle()
  for (let i = 0; i < n; i++) t.forward(size).right(360/n)
  return t.lines()
}

drawLines(shape(3, 120))  // triangle with 120mm sides
drawLines(shape(5, 80))  // pentagon with 80mm sides
```
</details>

If you were to `console.log(t.lines())` here and look in the developer console, you would see that the turtle figured out what polylines it effectively traced by following these instructions. Sometimes, this can be a lot easier than doing the math for yourself, although there's nothing to stop you! Here's another way to draw the same triangle as above:

```js
const size = 100
const angle = 120/180 * Math.PI

drawLines([
    [[0, 0], [0, size], [size * Math.sin(angle), size + size * Math.cos(angle)]]
])
```

Let's say that our first idea for drawing a feather is to draw a kind of stretched out hexagon for the vanes, and a rectangle for the shaft. The coordinates of the rectangle could be easy enough to define directly, but the hexagon might be tricky!

To practice using turtle commands, **see if you can draw your own shapes with turtles**. For the full list of turtle commands, see [the docs](/docs#Turtle). If you need a suggestion, maybe you could draw a blocky feather using a rectangle for the shaft and a kind of stretched out hexagon for the vanes, like this:



<details>
<summary>Show</summary>

Here's one of many approaches you could take:

```js
const shth = 3  // shaft thickness
const shl = 120  // shaft length
const cl = 30  // calamus length (part without vanes)
const vw = 20  // vane width, per vane
const t = new bt.Turtle()

// start pointing diagonally, and further within drawing area
t.left(45).jump([20, 20])

// draw the shaft
t.forward(shl).left(90).forward(shth).left(90)
t.forward(shl).left(90).forward(shth).left(90)

// move to start of vanes
t.up().forward(cl).left(90).forward(shth/2).right(90).down()

// draw vanes
const short = vw * Math.sqrt(2)
const long = shl - cl - 2 * vw

t.left(45)
t.forward(short).right(45).forward(long).right(45).forward(short)
.right(90)
t.forward(short).right(45).forward(long).right(45).forward(short)

drawLines(t.lines())
```

We have a lot of room for improvement, if we want this to be a realistic looking feather, but it's a good start!
</details>

### Transforming lines

Turtles may be good at drawing geometric shapes, but more interesting art pieces will often require curves, as well as more sophisticated ways to modify our lines after we've defined the basic form. 

The toolkit comes with a number of functions that operate over polylines, so for instance we can [`translate`](/docs/#translate) our lines to move them, [`rotate`](/docs/#rotate) to turn them all at once, [`scale`](/docs/#translate) to stretch them, and so on.

Here is an example that draws a 1x1 square, stretches it to a 50x80 rectangle, then centers it:

```js
const width = 125
const height = 125

setDocDimensions(width, height)

const sq = new bt.Turtle()
for (let i = 0; i < 4; i++) sq.forward(1).right(90)

const rect = bt.scale(sq.lines(), [50, 80])
bt.translate(rect, [width/2, height/2], bt.bounds(rect).cc)

drawLines(rect)
```

Notice that we used the [`bounds` function](/docs#bounds) here for the first time above, to find the bounds of center point of the rectangle and move that to the center of our document.

**See if you can also rotate the shape by 30 degrees**

While you're welcome to code in whatever style you prefer, you may find that using transform functions makes your code to be more flexible, allowing you to play more with the parameters and overall design.

As an example, consider the following reformulation of the feather code from above. By defining a `shape` function and just scaling shapes as needed, it's easier for us to do things like change the number of sides of the shapes, or their sizes:

```js
const width = 125
const height = 125

setDocDimensions(width, height)

// Generate any polygon
const shape = (n) => {
  const t = new bt.Turtle()
  for (let i = 0; i < n; i++) t.forward(1).right(360/n)
  return t.lines()
}

// Draw shaft as a stretched triangle
const shaft = bt.scale(shape(3), [2, 150])

// Draw vanes as a hendecagon (!?)
const vanes = bt.scale(shape(11), [8, 30])

// move the vanes to the end of the shaft
bt.translate(vanes, [0, bt.bounds(shaft).cb[1] - bt.bounds(vanes).cb[1]])

// combine the two shapes, then move and rotate them together!
// (this "destructuring" syntax in JavaScript combines the two arrays)
const feather = [...shaft, ...vanes]
bt.translate(feather, [width / 2, height / 2], bt.bounds(feather).cc)
bt.rotate(feather, 135)
drawLines(feather)
```

The above code draws the following feather:



This is another improvement, but still looking pretty rigid! **See if you can make some further transformations to help the feather look more natural**. One idea might be to use the [`iteratePoints`](/docs#iteratePoints) function to displace each point by a variable amount, to give the feather a bit of a bend.

<details>
<summary>Show</summary>

This approach uses `iteratePoints` to consider each [x, y] co-ordinate one by one, and change the x value by an amount that corresponds to its position. We can also [`resample`](/docs#resample) the points on our line (increase the number of points along the line) to emphasize this effect:

```js
// -- define and translate the feather, but don't rotate it yet

// resample, to increase number of points that we'll nudge
bt.resample(feather, 4)

// nudge the x value of each point, based on where it is in the doc, to make
// the whole thing curvy
bt.iteratePoints(feather, ([x, y]) => [x - 0.002*(width/2-y)*(width/2-y), y])

// -- now, rotate and draw it 
```

Adding the above code in the right place gives us the following:


</details>

### Drawing curves

While it was fun to use the word "hendecagon" above, it will often be preferable to draw curves directly, rather than composing increasingly complex turtle shapes. While Blot can only draw straight lines, if you draw enough small ones of them they'll start to pass for curves!

Thankfully there are toolkit functions to help us with this. Here's an example of using the [`catmullRom`](/docs#catmullRom) function, which tries to draw a nice curve passing through all the points you provide. Here we specify just 4 points, but end up drawing enough tiny line segments to see a curve:

```js
const width = 125
const height = 125

setDocDimensions(width, height)

const curve = bt.catmullRom([[0, 0], [30, 20], [50, 100], [125, 125]])

drawLines([curve])
```

Note that `bt.catmullRom` returns a single polyline, so we need to wrap it in a JavaScript array to pass it to `drawLines`. The above code generates this curve:



**Draw some more curves yourself, like a wave, or a wobbly circle thing. As a stretch goal, try re-writing the latest feather code using catmullRom or another [curve function](/docs#curves).**

<details>
<summary>Show</summary>
Here is a version of our feather drawing that uses Catmull-Rom spline to define a curve, instead of a many-sided polygon. We also take the opportunity to just define the shaft directly (since the turtle drawing was mainly to draw the vanes anyway) and to only resample the shaft, since the catmullRom uses numerous sample points already.

```js
const width = 125
const height = 125

setDocDimensions(width, height)

// Shaft is a stretched triangle
const shaft = bt.resample([[[0, 0], [1, 0], [0, -130], [-1, 0], [0, 0]]], 4)

// Vanes are a Catmull-Rom curve
const vanes = [bt.catmullRom([[0, 0], [-14, 16], [-22, 77], [0, 100], [15, 79], [14, 31], [0, 0]])]

// move the vanes nearer to the end of the shaft
bt.translate(vanes, [0, bt.bounds(shaft).cb[1] - bt.bounds(vanes).cb[1] - 8])

// combine the two shapes, then move and rotate them together!
const feather = [...shaft, ...vanes]
bt.translate(feather, [width / 2, height / 2], bt.bounds(feather).cc)
bt.iteratePoints(feather, ([x, y]) => [x - 0.002*(width/2-y)*(width/2-y), y])
bt.rotate(feather, 135)
drawLines(feather)
```

This short program gives us an impressively natural looking feather shape:


</details>

Once you start drawing curves, you'll want to keep going! As a stretch goal, **see if you can add barbs to the feather, or otherwise make it more realistic**.

<details>
<summary>Show</summary>

By iterating over the points in our shaft, we can draw individual barbs as their own Catmull-Rom splines. We can then use the vane definition not to draw a vane, but to mask out the barbs using [cut](/docs#cut).

```js
const width = 125
const height = 125

setDocDimensions(width, height)

// Shaft is a stretched triangle
const shaft = bt.resample([[[0, 0], [1, 0], [0, -130], [-1, 0], [0, 0]]], 1)

// Vanes are a Catmull-Rom curve
const vanes = [bt.catmullRom([[0, 0], [-14, 16], [-22, 77], [0, 100], [15, 79], [14, 31], [0, 0]])]

// Barbs are Catmull-Rom curves originating at the shaft
const barbs = []
for (let i = 0; i < shaft[0].length; i++) {
  const parity = i > shaft[0].length/2 ? -1 : 1
  const [x, y] = shaft[0][i]
  barbs.push(bt.catmullRom(
    [[x, y], [x + parity * 10, y - 2], [x + parity * 30, y]]))
}

// move the vanes nearer to the end of the shaft
bt.translate(vanes, [0, bt.bounds(shaft).cb[1] - bt.bounds(vanes).cb[1]])

// Use the vane shape to trim the barbs!
bt.cut(barbs, vanes)

// combine the two shapes, then move and rotate them together!
const feather = [...shaft, ...barbs]
bt.translate(feather, [width / 2, height / 2], bt.bounds(feather).cc)
bt.iteratePoints(feather, ([x, y]) => [x - 0.002*(width/2-y)*(width/2-y), y])
bt.rotate(feather, 135)
drawLines(feather)
```

Progress!



</details>

### Randomness

If our art piece feels a little boring at this point, it may be because we haven't done anything random! Using randomness in our programs can add interest to an individual piece by modeling a more natural process, but it can also turn our static piece into something more generative, that can draw a different variant of the work each time we hit "refresh".

**Using toolkit functions like [randInRange](/docs#randInRange), modify the piece to generate a new, interesting feather each time!**

Once you're comfortable with the [randomness](/docs#randomness) functions, you'll want to use them extensively, since the results can be much more interesting!



<details>
<summary>Show code</summary>

Below is one approach that chooses some parameters within random ranges, and also randomly "clumps" together some of the barbs:

```js
const width = 125
const height = 125

setDocDimensions(width, height)

const rr = bt.randInRange

const shaftLength = rr(0.5, 0.8) * Math.sqrt(width * width + height * height)
const vaneLength = rr(0.7, 0.8) * shaftLength
const vaneWidth = rr(0.2, 0.3) * vaneLength
const barbCurviness = rr(1, 4)
const numClumps = rr(1, 6)

const shaft = bt.resample([[[0, 0], [0.8, 0], [0, -shaftLength], [-0.8, 0], [0, 0]]], 1)

const vanes = bt.scale([bt.catmullRom([
  [0, 0],
  [rr(-1, -0.5), rr(0.15, 0.3)],
  [rr(-1, -0.5), rr(0.7, 0.9)],
  [0, 1],
  [rr(0.5, 1), rr(0.7, 0.9)],
  [rr(0.5, 1), rr(0.15, 0.3)],
  [0, 0]
])], [vaneWidth, vaneLength])

// Barbs are Catmull-Rom curves originating at the shaft
const barbs = []
const len = shaft[0].length
for (let i = 0; i < len; i++) {
  const parity = i > len / 2 ? -1 : 1
  const [x, y] = shaft[0][i]
  barbs.push(bt.catmullRom([
    [x, y],
    [x + parity * vaneWidth * 0.3, y - barbCurviness],
    [x + parity * vaneWidth, y]
  ], 5))
}

// move the vanes to the end of the shaft
bt.translate(vanes, [0, bt.bounds(shaft).cb[1] - bt.bounds(vanes).cb[1]])

// Use the vane shape to trim the barbs!
bt.cut(barbs, vanes)

// Clump some of the trimmed barbs together, like nature intended
for (let i = 0; i < numClumps; i++) {
  const numBarbs = Math.floor(rr(3, 20))
  const start = Math.floor(rr(0, barbs.length - numBarbs))
  const target = barbs[Math.floor(start + rr(0, numBarbs))]
  for (let j = 0; j <= numBarbs; j++) {
    const barb = barbs[start + j]
    const t = j / numBarbs
    const [tx, ty] = target[Math.floor((target.length - 1) * 0.9)]
    const [bx, by] = barb[Math.floor((barb.length - 1) * 0.9)]
    const mid = [tx * (1 - t) + bx * t, ty * (1 - t) + by * t] 
    barbs[start + j] = bt.catmullRom([
      barb[0],
      mid,
      target[target.length-1]
    ], 10)
  }
}

// combine the shaft with the barbs
const feather = [...shaft, ...barbs]
bt.translate(feather, [width / 2, height / 2], bt.bounds(feather).cc)
bt.iteratePoints(feather, ([x, y]) => [x - 0.001*(width/2-y)*(width/2-y), y])
bt.rotate(feather, bt.randInRange(120, 150))
drawLines(feather)
```

</details>

### Next steps

This tutorial was just a brief introduction to how Blot works, and to some of the toolkit functions. From here, you may want to just try to implement your own ideas using [the docs](/docs) as needed. Or, take a look at one of the many [user-contributed guides](/guides). Once you're happy with a piece, be sure to share it! Have fun!

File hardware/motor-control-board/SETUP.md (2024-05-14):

# Firmware

assembled control board with annotations

You'll need a computer with the Arduino IDE installed, as well as the control board and a USB-C cable. After following these steps, you'll be set up to use your motor control board to interface with your new drawing machine.

## Hardware setup

Hold the `B` (BOOT) button on the XIAO board and plug it in to your computer.



The "RPI-RP2" disk should show up on your computer if the above step was successful.

disk in macos finder

## Software setup

> You'll need to have the latest version of the Arduino IDE installed. [Install it here.](https://www.arduino.cc/en/software/)

1. Open the Arduino IDE.
2. Add the Seeed Studio XIAO RP2040 board package to your IDE. Navigate to **Arduino IDE** > **Settings...** and add the following URLs to the **Additional Board Manager URLs** field. It's a single line, so you should combine the URLs with a comma.

```
https://github.com/earlephilhower/arduino-pico/releases/download/global/package_rp2040_index.json
https://raw.githubusercontent.com/qbolsee/ArduinoCore-fab-sam/master/json/package_Fab_SAM_index.json
```

4. Navigate to **Tools** > **Board** > **Boards Manager**, and search for "rp2040". Install the latest version of "Raspberry Pi Pico/RP2040" (author Earle F. Philhower, III).

rp2040 in boards manager

5. Now that you have the board package installed, you can upload the firmware to the board. Select your board and port in **Tools** > **Board** and find "**Seeed Studio XIAO RP2040**.

select board

To select the port, go to **Tools** > **Port** and select the serial port name of the connected board.

select serial port

> Then, install the following libraries via Arduino's library manager:
>
> - FlashStorage_SAMD (by Cristian Maglie, Khoi Hoang)
> - AccelStepper (by Mike McCauley)
> - osap (by Jake Robert Read)

1. Copy the Arduino code from the respective firmware file (found in [`./firmware`](./firmware/)) into your IDE and upload to your board.

> The firmware is very fresh and poorly documented (and rapidly changing). Ask in #haxidraw-developemnt for a link to the latest version.

Upload firmware to board

> Now you can write your own web interface and use it to control your machine. Check out some example [interfaces](../interfaces/) which are open source on GitHub.

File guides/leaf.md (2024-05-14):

---
title: How to draw a leaf
thumbnail: https://cloud-7rdff2vjy-hack-club-bot.vercel.app/0250635645-9ce96217-bc5e-49cc-87b2-178681188eb3.webp
contributors: leomcelroy
---

> You can follow along in this editor: https://blot.hackclub.com/editor?guide=leaf

---

Let's learn how to draw a leaf that looks likes this.

leaf

Let's break it down into parts.

## Outline

We'll start with the outline of the leaf.



First let's lay down a line which will become the top edge.

```js
// welcome to blot!

const width = 125;
const height = 125;

setDocDimensions(width, height);

const leafLength = 5
const leafW = 1.8

const finalLines = [];

const topEdge = [
  [
    [0, 0],
    [leafLength*0.3, leafW],
    [leafLength*0.8, leafW*.01],
    [leafLength, 0]
  ]
]

bt.join(finalLines, topEdge);

// center piece
const finalBounds = bt.bounds(finalLines);
const finalScale = width/finalBounds.width*.85;
bt.scale(finalLines, finalScale);
bt.translate(finalLines, [width / 2, height / 2], bt.bounds(finalLines).cc);

// draw it
drawLines(finalLines);
```



We can make this line smooth using a NURBS curve.

```js
const topEdge = [
  bt.nurbs([
    [0, 0],
    [leafLength*0.3, leafW],
    [leafLength*0.8, leafW*.01],
    [leafLength, 0]
  ])
]
```



Let's make the bottom edge too.

```js
...

const topEdge = [
  bt.nurbs([
    [0, 0],
    [leafLength*0.3, leafW],
    [leafLength*0.8, leafW*.01],
    [leafLength, 0]
  ])
]

// add our code here
const bottomEdge = bt.copy(topEdge);
bt.scale(bottomEdge, [1, -1], [0, 0]);
bt.join(finalLines, bottomEdge);

bt.join(finalLines, topEdge);

...
```



Now we can add some noise to make the leaf look a bit more organic.

```js
bt.iteratePoints(topEdge, (pt, t) => {
  const [x, y] = pt;
  const freq = 2.84;
  const dy = bt.noise(t * 20.4, { octaves: 2 }) * 0.15 * (t === 0 || t === 1 ? 0 : 1)
  return [x, y + dy]
})

bt.iteratePoints(bottomEdge, (pt, t) => {
  const [x, y] = pt;
  const dy = bt.noise(t * 20.8, { octaves: 2 }) * -0.2 * (t === 0 || t === 1 ? 0 : 1)
  return [x, y + dy]
})

bt.join(finalLines, topEdge);

...
```

This term `(t===0 || t === 1 ? 0 : 1)` makes sure that the endpoints stay the same on the curve.
Try playing with the multiplication terms.



Now we have an outline let's do the veins of the leaf.

## Veins

After adding the veins our leaf will look like this.



We'll start with the top side by drawing some lines the follow the distribution of the edge.
Let's make a veins function which will return some lines we can add to our main drawing.

```js

function makeVeins() {
  const veins = [];

  let littleLinesMax = 61
  for (let i = 4; i < littleLinesMax - 5; i++) {
    const t = i / (littleLinesMax - 1); // this line to get t values 0 to 1 while iterating is very common
    const x0 = t * leafLength;
    const y0 = 0;
  
    const y = bt.getPoint(topEdge, t + 0.1)[1]
  
    const angle = (-70 + t * 37 + bt.randInRange(-4, 4)) / 180 * Math.PI;
    let r = y * 0.8;
  
    const line = [
      bt.nurbs([
        [x0, y0],
        [
          x0 + Math.cos(angle) * r / 2 - y / 4,
          -(y0 + Math.sin(angle) * r / 2)
        ],
        [
          x0 + Math.cos(angle) * r,
          -(y0 + Math.sin(angle) * r)
        ]
      ])
    ];
  
    if (r < 0.01) continue;
  
    bt.join(veins, line);
  }

  return veins;
}
```

Which we can add to the drawing like such:

```js
bt.join(finalLines, makeVeins());
```



Let's randomly trim each vein with every fifth being a bite longer.

```js
if (r < 0.01) continue;

// the ternary makes evey fifth line trimmed up to 0.7 to 0.9 and all the others between 0.1 and 0.7
const trimTo = (i % 5 === 0) ?
  bt.randInRange(0.7, 0.9) :
  bt.randInRange(0.1, 0.7);

bt.trim(line, 0, trimTo);

```



And let's randomly break up these lines.

```js
bt.resample(line, .03);

bt.iteratePoints(line, pt => {
  return Math.random() < (i % 5 === 0 ? 0.28 : 0.40) ? 'BREAK' : pt;
});
```



Then call veins again and flip it over for the bottom side.

```js
const bottomVeins = makeVeins();
bt.scale(bottomVeins, [1, -1], [0, 0]);
bt.join(finalLines, bottomVeins);
```



## The Stem

The stem is the easiest part.

We just need to draw a line.

```js
const stem = [
  [
    [-leafLength*.2, 0],
    [leafLength, 0]
  ]
];
bt.resample(stem, 0.01);
bt.join(finalLines, stem);
```



## Finishing Up

To Finish our leaf let's go through all the points and add a little noise and a bend upwards.

```js
bt.iteratePoints(finalLines, pt => {
  let [x, y] = pt
  y += x * x * 0.02
  y += bt.noise([x * 0.2]) * 0.3
  return [x, y]
});
```

And now we have a leaf!



## Acknowledgements

Thanks to [Lingdong](https://github.com/LingDong-) for drawing the first draft of the leaf with me.

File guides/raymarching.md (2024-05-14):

---
title: Raymarching in Blot
thumbnail: https://cloud-79ah2o72z-hack-club-bot.vercel.app/00image.webp
contributors: henrybass
pinned: true
---

The goal of this guide will be to simulate 3D environments, with realistic lighting and shadows. By the end, you should have something like this:

Raymarching in Blot

Let's start by thinking about how vision works in real life. Light rays come from sources such as the sun, bounce around, and eventually, some of them arrive at our eyes. We could simulate each ray coming from the light source, but this would be really slow. Most light rays miss our eyes, resulting in many redundant calculations. A better approach is to simulate the process of vision in reverse:

- Shoot light rays from the camera
- Find where and what they hit
- From there, cast them in the direction of a light source, to see if they're in a shadow

wikipedia image

The next obvious problem is exactly how to determine if each ray actually hits any objects in the scene. In typical ray tracing, this is done with defined intersection functions for each object: That function directly determines where a given ray will intersect some surface. To render objects with complex geometry, you often have to break those objects down into smaller building blocks for which you already know an intersection function. The problem is, this can be quite slow.

Luckily, an alternative exists. In ray marching, there's no need to have an intersection function. Instead, we can use something called a Signed Distance Field, or SDF. This, instead of directly telling us if a given ray will intersect an object, simply tells us how far the ray is from the closest point of that object. From there, we can use the following algorithm:

- Find how far a ray is from the nearest object
- Move the ray forwards by that distance, as we know that that's the farthest it can go without having a chance of hitting anything
- If the new minimum distance is below some low threshold, the ray has probably hit some object. Otherwise, repeat this sequence of steps until it does hit something.

wikipedia image

Then, once we've hit an object, we should cast a ray at each light source. If the ray hits some object on its way to a light source, then it should be a shadow. Otherwise, it's illuminated.

We can then do a few more calculations to determine exactly how dark it should be shaded, and then finally we draw it to the screen.

With the basic algorithm planned, let's start writing code.

First, initialize a turtle:
`const t = new Turtle()`

### Then, let's start defining some objects.

A Vec3, or 3 dimensional [vector](<https://en.wikipedia.org/wiki/Vector_(mathematics_and_physics)>), is a mathmatical object with some position. You can think of it as a set of 3 numbers, pointing to some location in space. They're a fundimental object in linear algebra, a mathematical subject used heavily in 3D graphics. For a good introduction to linear algebra, watch the first few episodes of [Essence of Linear Algebra](https://www.youtube.com/watch?v=fNk_zzaMoSs&list=PLZHQObOWTQDPD3MizzM2xVFitgF8hE_ab) by 3Blue1Brown.

There are a few basic functions we'll want to use with vectors:

- Vectors can be added and subtracted, which corresponds to adding and subtracting each of their components.

- We'll also want to find the distance between 2 vectors. This is done with a 3D generalization of the [Pythagorian Theorem.](https://en.wikipedia.org/wiki/Pythagorean_theorem) You can think of this as finding the hypotenuse of a triangle where the position of each vector corresponds to a vertex.
- Vectors can be scaled by [scalars](<https://en.wikipedia.org/wiki/Scalar_(mathematics)>), which are essentially just ordinary numbers. This is done by multiplying each component of the vector by the scalar, effectively expanding or shrinking it.
- We also need to know how large a vector is. This is done by just finding the distance between the vector and the point 0, 0, 0.
- When a vector is normalized, we're scaling it down or up to be a [Unit Vector.](https://en.wikipedia.org/wiki/Unit_vector) We do this when we only care about the direction of a vector, not how large it is. This is done by dividing it by its size.
- Lastly, we'll want a way to compute the [Dot Product](https://en.wikipedia.org/wiki/Dot_product) of two vectors. This is an operation that takes in 2 vectors and returns a scalar corresponding to how parallel they are. If two vectors are perpendicular, the dot product is zero. If they're parallel, the dot product is 1. This is done by multiplying each of the components of one vector by each component of another, and then adding the results together.

In code, that class looks like this:

```js
class Vec3 {
  constructor(x, y, z) {
    this.x = x
    this.y = y
    this.z = z
  }

  add(other) {
    return new Vec3(other.x + this.x, other.y + this.y, other.z + this.z)
  }

  subtract(other) {
    return new Vec3(this.x - other.x, this.y - other.y, this.z - other.z)
  }

  dist(other) {
    return Math.sqrt(
      (other.x - this.x) ** 2 +
        (other.y - this.y) ** 2 +
        (other.z - this.z) ** 2
    )
  }

  scale(scalar) {
    return new Vec3(this.x * scalar, this.y * scalar, this.z * scalar)
  }

  magnitude() {
    return this.dist(new Vec3(0, 0, 0))
  }

  normalized() {
    return this.scale(1 / this.magnitude())
  }

  dot(other) {
    return this.x * other.x + this.y * other.y + this.z * other.z
  }
}
```

Great! Now we can get to defining the physical objects in the scene. Each one should hold a position, an SDF, and optionally other attributes like size.

A sphere is simple:

The SDF is just the distance between a given point and the center, minus the radius.

```js
class Sphere {
  constructor(pos, radius) {
    this.pos = pos
    this.radius = radius
  }

  SDF(pos) {
    return pos.dist(this.pos) - this.radius
  }
}
```

Visually, in 2D, the Signed Distance Field looks like this:



Next, here's a cube:

```js
class Cube {
  constructor(pos, size) {
    this.pos = pos
    this.size = size
  }

  SDF(pos) {
    return (
      Math.max(
        Math.abs(pos.x - this.pos.x),
        Math.abs(pos.y - this.pos.y),
        Math.abs(pos.z - this.pos.z)
      ) - this.size
    )
  }
}
```

The cube SDF simply finds the distance between the cube and a given position in the x, y, and z direction, and takes the maximum. Lastly, we subtract the size. This is quite similar to the SDF of a sphere, but instead of computing the distance in 3D with the Pythagorean Theorem, we compute the 1-dimensional distance 3 times.

Next, let's define planes. The only important attribute these have is a y value, as they extend infinitely in every direction. The SDF is also very simple, as it's just the vertical distance between a given point and the plane.

```js
class Plane {
  constructor(pos) {
    this.pos = pos
  }

  SDF(pos) {
    return pos.y - this.pos.y
  }
}
```

If you want, you can define more complex objects too. For example, here's a sphere distorted by [noise](https://en.wikipedia.org/wiki/Gradient_noise). It's identical to a sphere, except for the fact that we randomly disturb the SDF with the Haxidraw editor's built-in fractal noise function. We'll also want to offset the noise sample by some constants, to make it asymmetrical.

```js
class NoisySphere {
  constructor(pos, radius, noiseScale, noiseAmp) {
    this.pos = pos
    this.radius = radius
    this.noiseScale = noiseScale
    this.noiseAmp = noiseAmp
  }

  SDF(pos) {
    return (
      pos.dist(this.pos) -
      this.radius +
      this.noiseAmp *
        noise([
          pos.x * this.noiseScale + 10,
          pos.y * this.noiseScale - 7,
          pos.z * this.noiseScale + 2
        ])
    )
  }
}
```

Those are all the primitive objects we need. From there, we can start defining the other classes, like `LightSource`.

All a light source needs is a position, and radius.

```js
class LightSource {
  constructor(pos, size) {
    this.pos = pos
    this.size = size
  }
}
```

To hold all these things, we can store them in a world object:

```js
class World {
  constructor(objects, lightsources) {
    this.objects = objects
    this.lightsources = lightsources
  }
}
```

The ray is the most important object in raymarching. It's going to hold the logic for marching forwards, and determining if it hits anything.

First, give it a position and direction. These will both be of the class Vec3, as they'll point to a location in 3D space.

```js
class Ray {
    constructor (pos, dir) {
        this.pos = pos
        this.dir = dir
    }
```

The travel function will move the ray along its direction by a given distance. We do this by adding its direction to its position, scaled by the distance we want to travel.

```js
    travel(dist) {
        this.pos = this.pos.add(this.dir.scale(dist))
    }
```

Now, for the cast function. First, take in a camera (we'll define cameras later), and the objects the ray can collide with.

```js
    cast(objects, camera) {
```

Then, we'll need some variables. The `closestDist` records the distance to the nearest object we've found so far. We can set this to infinity when we first start out.

```js
let closestDist = Infinity
```

The `minDist` stores exactly how close a ray should be to an object before we count it as being a hit. Likewise, the `maxDist` is how far the ray can be from the camera before we give up on marching it.

```js
let minDist = 0.01
let maxDist = camera.clipDist
```

The `hitObj` is the current closest object we've found. It's null to start, because we haven't found any objects yet.

```js
let hitObj = null
```

Here's the main loop. As long as the ray hasn't yet collided with anything, and is within range of the camera, we'll check for collisions. We do this by iterating through each object, and using its SDF to find how far away we are. If the current object is the new closest one found, we set it to be our hit object. Then, we travel forward by the closest distance found in the last step.

```js
while (closestDist > minDist && this.pos.dist(camera.pos) < maxDist) {
  closestDist = Infinity
  for (let obj in objects) {
    let dist = objects[obj].SDF(this.pos)
    if (dist < closestDist) {
      closestDist = dist
      hitObj = objects[obj]
    }
  }
  this.travel(closestDist)
}
```

At the end, we'll return all the important information:

- If we hit something
- What we hit
- Where we hit it

```js
        return [closestDist < minDist, hitObj, this.pos]
    }
```

The next function is almost identical to the first. The difference is that here, we're not just looking for hits with any object - we're seeing if it hits a specific one. The point of this function is to check for collisions with light sources, so that we can determine if a given point is in shadow. We also move forwards by a small distance to start with, so that we don't collide with our start object.

The ray marches along, returning false if it collides with something other than the target, and returning true if it's close enough to the target.

```js
    getTarget(target, objects, camera) {
        let closestDist = Infinity
        let minDist = 0.05
        let maxDist = 80
        let hitObj = null
        this.travel(0.01)
        while ((closestDist > minDist) && (this.pos.dist(camera.pos) < maxDist)) {
            for (let obj in objects) {
                let dist = objects[obj].SDF(this.pos)
                if (dist < closestDist) {
                    closestDist = dist
                    hitObj = objects[obj]
                }
            }
            let dist = target.dist(this.pos)
                if (dist < 0.1) {
                    return true
                }
            this.travel(0.05 * closestDist)

        }
        return false
    }
}
```

### There's one more utility function we'll want:

To shade objects later, we're going to need a way to find their [normal vectors](<https://en.wikipedia.org/wiki/Normal_(geometry)>). A normal is a vector pointing directly away from some surface.



Because we already know the SDF of a given object, this is actually quite easy. The normal is simply an arrow pointing along the gradient of our signed distance field.

To imagine this, take the diagram below, and reverse the direction of the arrows. Each arrow points in the direction of the SDF gradient. Each arrow is effectively the normal vector to that point in 3D space, relative to the SDF.


To find these arrows, we'll just need to determine the local "slope" of the SDF -
if you know calculus, we're basically taking the derivative in 3D. We'll determine
how the SDF changes in response to a really small nudge in the x, y, and z directions.
We then subtract that from the SDF at our start position, giving us the rate of change
in each direction. Finally, we normalize this, to get the normal vector.

```js
function computeNormal(pos, obj) {
  let startSDF = obj.SDF(pos)
  return new Vec3(
    obj.SDF(pos.add(new Vec3(0.001, 0, 0))) - startSDF,
    obj.SDF(pos.add(new Vec3(0, 0.001, 0))) - startSDF,
    obj.SDF(pos.add(new Vec3(0, 0, 0.001))) - startSDF
  ).normalized()
}
```

### Next, let's define the camera.

The camera should first obviously have a position. Next, a field-of-view value. Lastly, a clip distance, to determine how far it can see.

```js
class Camera {
    constructor(pos, fov, clipDist) {
        this.pos = pos
        this.fov = fov
        this.clipDist = clipDist
    }
```

It aalso needs to have a `getRay` function, responsible for actually casting a ray. It points a ray at a given x and y, then shoots it in that direction.

This is the function that enables the camera to "look" in the direction of a given pixel.

Conceptually, you can think of it like this:

- For a given pixel, match it to a point in 3D space. The x and y of the pixel in the screen will correspond to a physical x and y point on a plane in front of the camera. We then cast the ray in that direction, and render it to the screen depending on what it hits:



Here's it in code:

```js
    getRay(x, y, world) {
      let ray = new Ray(this.pos, new Vec3(x, y, this.fov))
      return ray.cast(world.objects, this)
    }
```

Next, the `getShadow` function. This takes a point in 3D space, and shoots it at every light source, one at a time. To get realistically blurred shadows, we can aim at a random point within the bounds of the light source, instead of its exact center.

```js
    getShadow(pos, world) {
      for (let i in world.lightSources) {
        let size = world.lightSources[i].size
        let randOffset = new Vec3(Math.random() * size, Math.random() * size, Math.random() * size)
        let diff = world.lightSources[i].pos.add(randOffset).subtract(pos)
        let ray = new Ray(pos, diff)
```

Here's where we actually use `getTarget`. We start by pointing the ray at the light source, plus a random offset within the volume of the light source. Then, we check if it ever reaches that source. If it's a hit, break the loop and return true, otherwise keep iterating through light sources. At the end, if none have been found, return false.

```js
        if (ray.getTarget(world.lightSources[i].pos.add(randOffset), world.objects, this)) return true
      }
      return false
    }
}
```

And that's the camera object!

### So, how do we draw this to the screen?

This whole time, we haven't done much Haxidraw-specific code at all. To actually draw the output, we'll need a way of representing a pixel as a turtle path. To do this, we can use a process called [dithering.](https://en.wikipedia.org/wiki/Dither) Let's take a closer look at the original image, to see how this is used:



Each "_pixel_" is just a set of lines. Darker pixels have 2 lines, and white pixels have none. Zooming out far enough, this gives the illusion of smooth gradients.

Because we only have 3 possible discrete brightness levels, we have to use some randomness to give the illusion of a wider range of colors from farther away. For example, although there appear to be various shades of grey in the below image, each pixel is actually only black or white. The value is determined probabilistically, where pixels that should be shaded darker have a higher probability of being black.



Here's what that looks like in the code:

- We go to the x and y values of the pixel.
- If the brightness is lower than a random value, draw a forward slash.
- If it's below another lower threshold, draw a backslash.

```js
function drawPixel(x, y, w, h, brightness) {
  t.up()
  t.goTo([x, y])
  t.down()
  if (brightness < Math.random()) {
    t.goTo([x + w, y + h])
    t.goTo([x, y])
    if (brightness < Math.random() * 0.5) {
      t.goTo([x + w, y])
      t.goTo([x, y + h])
      t.goTo([x + w, y + h])
      t.goTo([x, y])
    }
  }
}
```

### We're ready to build our main render function!

We can define the screen dimensions:

```js
const screenWidth = 3
const screenHeight = 2
```

And then the pixel size: (Tweak this whenever you want, to change the detail of the image! Lower numbers render slower.)

```js
const dx = 0.005
const dy = 0.005
```

```js
function renderFrame(camera) {
  for (let y = -screenHeight/2; y < screenHeight/2; y+= dy) {
    for (let x = -screenWidth/2; x < screenHeight/2; x+= dx) {
```

At each point, we'll get the corrosponding ray at that pixel:

```js
      let [hit, hitObj, rayPos] = camera.getRay(x, y, world)
      if (hit) {
```

If we're hit something, we'll check if there's a shadow at that hit location:

```js
        let noShadow = camera.getShadow(rayPos, world)
        let brightness = 0;
        if (noShadow) {
```

If there was a shadow, we can leave the brightness at zero - no light is hitting it. _(In real life, there's diffuse ambient lighting, but we're not accounting for that)_. If there wasn't a shadow, that doesn't mean the pixel should be 100% bright, though.

If the vector from the light to the hit point and the normal of the surface are parallel, then the hit point is very directly illuminated. On the other hand, if the two vectors are perpendicular, then we shouldn't shade the point very brightly. We can use the dot product to determine exactly how parallel or perpendicular these vectors actually are.



```js
let norm = computeNormal(rayPos, hitObj)
```

Iterate through light sources, adding the brightness from each. The brightness is the normalized dot product between the normal and a vector pointing from the light source to the ray position:

```js
for (let i in world.lightSources) {
  brightness += norm.dot(
    world.lightSources[i].pos.subtract(rayPos).normalized()
  )
}
```

Average them out at the end:

```js
          brightness /= world.lightSources.length
        }
```

Draw a pixel with that brightness. If we didn't hit something with the ray at the start, we just skip drawing anything.

```js
        drawPixel(x, y, dx, dy, brightness)
      } else {
        t.up()
        t.goTo([x, y])
      }
    }
```

Go back to the left to render the next line:

```js
    t.up()
    t.goTo([-3, 0])
    t.down()
  }
}
```

And now, finally, we can create a world, and render it! Here, we initialize our camera, light sources, and objects. The parameters are arbitrary, and you can shift them around or add different objects to create any scene you want.

```js
const cam = new Camera(new Vec3(0, 0, 0), 1.0, 20)
const world = new World()
world.lightSources = [new LightSource(new Vec3(20, 10, -5), 5)]
world.objects = [
  new Cube(new Vec3(-2.09, -2, 9.2), 1),
  new Cube(new Vec3(-4.9, -2, 6.3), 1),
  new Cube(new Vec3(1.2, -2, 7.2), 1),
  new Plane(new Vec3(0, -3, 0))
]
renderFrame(cam)
drawTurtles(t)
```

Great job! If all went well, you should have a working 3D renderer for the Haxidraw. It's capable of rendering any shape with a defined SDF, so there are plenty of possibilities to explore. Here are a few scenes I've created with the engine:




The result of an interesting graphical glitch:



And there are plenty more possibilities! In fact, the engine as provided in this guide is quite minimal, and there are plenty of changes that can be made to make it more advanced. Here are a few ideas:

- Add reflections: This can be done by casting another ray from the hit position into the surroundings, and adding the color of the object it hits to the original object.

- Diffuse lighting: This can be done similarly to reflections, by casting many rays randomly from the original ray's hit position, and letting them scatter around the environment. Then, add the average color back to the original object.

- Depth of field: When shooting rays from the camera, first make them pass through a focal point, offset randomly. This should give an adjustable depth-blur effect.

- Try rendering more objects! Plenty of complex shapes have simple SDFs, for example, the amazing [Mandelbulb](https://en.wikipedia.org/wiki/Mandelbulb).

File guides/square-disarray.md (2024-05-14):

---
title: Square Disarray
thumbnail: https://cloud-qogbw3upi-hack-club-bot.vercel.app/0260524306-bcaf04e7-a00e-4f98-aaed-01eeebf2c79c.webp
contributors: leomcelroy
---

> You can follow along in [this editor](https://blot.hackclub.com/editor?guide=square-disarray).

Let's something like draw this:

square disarray

# Setting Up Workarea

Let's start by centering the drawing we'll make in the document.

```js
/*
there are three built in names

setDocDimensions
drawLines
blotToolkit (also called bt)

the toolkit has lots of useful functions we can access
*/

const width = 120;
const height = 120;

setDocDimensions(width, height);

const finalLines = []; // we will put our shapes here

// let's get the bounds of our final lines
const finalLinesBounds = bt.bounds(finalLines);

// this moves the center of our drawing to the center of our doc
bt.translate(
  finalLines,
  [ width / 2, height / 2 ], 
  finalLinesBounds.cc
); 

drawLines(finalLines);
```

# Draw a Square

This function draws rectangles.

```js
function rect(w, h) {

  // notice how this is an array of arrays
  return [
    [
      [-w/2, h/2],
      [w/2, h/2],
      [w/2, -h/2],
      [-w/2, -h/2],
      [-w/2, h/2],
    ]
  ]
}
```

Let's use it to add a square to our drawing.



<details>
<summary>Hint</summary>
  
```js
// ...

const finalLines = []; // we will put our shapes here

bt.join(finalLines, rect(10, 10)); // here is the new line

// ...
```

</details>

# Make a Grid

First we'll make a row. Start with a lot of squares.

```js
const gridWidth = 10

for (let i = 0; i < gridWidth; i++) {
  const square = rect(10, 10);
  bt.join(finalLines, square);
}
```



We can't see any change because they are on top of eachother! Space them out.



<details>
<summary>Hint</summary>

```js
for (let i = 0; i < 3; i++) {
  const square = rect(10, 10);
  bt.translate(square, [23 * i, 0]);
  bt.join(finalLines, square);
}
```

</details>

If we want the spacing to be perfect, each square should move by the width of a square.



<details>
<summary>Hint</summary>

```js
const squareWidth = 10
for (let i = 0; i < 3; i++) {
  const square = rect(squareWidth, 10);
  bt.translate(square, [squareWidth * i, 0]);
  bt.join(finalLines, square);
}
```

</details>

To make it a grid add another loop.



<details>
<summary>Hint</summary>

```js
const squareWidth = 10
const squareHeight = 10
for (let i = 0; i < 3; i++) {
  for (let j = 0; j < 3; j++) {
    const square = rect(squareWidth, squareHeight)
    bt.translate(square, [squareWidth * i, squareHeight * j])
    bt.join(finalLines, square);
  }
}
```

</details>

Increase the loop range for a bigger grid.



# Add Some Disarray

We can randomly translate each square.



<details>
<summary>Hint</summary>
  
```js
for (let i = 0; i < 10; i++) {
  for (let j = 0; j < 10; j++) {
    const square = rect(squareWidth, squareHeight);
    bt.translate(
      square, 
      [
        squareWidth * i, 
        squareHeight * j
      ]
    );

    // randomness added here
    bt.translate(
      square, 
      [
        bt.randInRange(-1, 1), 
        bt.randInRange(-1, 1)
      ]
    );

    bt.join(finalLines, square);
  }
}
```

</details>

Scale the randomness with the x location.



<details>
<summary>Hint</summary>
  
```js
bt.translate(square, [(bt.randInRange(-1, 1) * i) / 6, (bt.randInRange(-1, 1) * i) / 6])
```

</details>

Now rotate each square in a similar manner.



<details>
<summary>Hint</summary>

```js
bt.rotate(square, bt.randInRange(-1, 1) * 2 * i)
```

</details>

And that's our piece!

# Extensions

- Can you adjust transformations based on x and y?
- Can you add scale to the transformations?
- Can you change the rectangle sizes?

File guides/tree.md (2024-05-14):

---
title: Let's draw a tree
thumbnail: https://github.com/hackclub/haxidraw/assets/27078897/b2b3b319-1b0f-4c0e-bf78-d8323ab577d4
---

> You can follow along in this editor: [https://blot.hackclub.com/editor/
](https://blot.hackclub.com/editor?guide=tree)
We're going to use abstract scribbles to make a tree that looks like this.



## the trunk



Let's look at that a bit closer.



To start the trunk let's draw some lines.

```js
let trunk = createTurtle();

// notice this pattern of using t which is 0 to 1
let iMax = 3; // the number of lines
for (let i = 0; i < iMax; i++) {
  const t = i / (iMax - 1);
  const x = t * 0.6; // this factor sets the spacing
  const trunkLine = createTurtle([x, 0]);
  trunkLine.left(90);

  trunkLine.forward(2.8);

  trunk.join(trunkLine);
}

// ...

renderTurtles(trunk);
```



Now let's reach for the secret ingredient, perlin noise.

```js
trunkLine
  .forward(2.8)
  .resample(0.02) // we resample so we have points to move
  .iteratePath((pt, tValue) => {
    const [x, y] = pt;
    pt[0] += noise(y * 1.8) * -0.3; // shake them up a little
    pt[0] += Math.sin(y * 0.05); // give a little curve
  });
```



We add a few more lines and make a gradient by filtering more out to the right.

```js
.iteratePath((pt, tValue) => {
  const [ x, y ] = pt;
  pt[0] += noise(y*1.8)*-0.3; // shake them up a little
  pt[0] += Math.sin(y*0.05);  // give a little curve

  if (rand() < t*0.44) return "BREAK"; // filter out points
})
```



Keep the first and last line solid.

```js
.iteratePath((pt, tValue) => {
  const [ x, y ] = pt;
  pt[0] += noise(y*1.8)*-0.3; // shake them up a little
  pt[0] += Math.sin(y*0.05);  // give a little curve

  if (t === 0 || t === 1) return pt; // keep the first and last lines solid
  if (rand() < t*0.44) return "BREAK"; // filter out points
})
```



Fade the trunk out towards the leaves.

```js
.iteratePath((pt, tValue) => {
  const [ x, y ] = pt;
  pt[0] += noise(y*1.8)*-0.3; // shake them up a little
  pt[0] += Math.sin(y*0.05);  // give a little curve

  if (t === 0 || t === 1) return pt; // keep the first and last lines solid
  if (rand() < lerp(0, 1, 0.54*tValue**2)) return "BREAK"; // fade the trunk out towards the leaves
  if (rand() < t*0.44) return "BREAK"; // filter out points
})
```



Then a little y-displacement so the bottom isn't unnatural looking

```js
const trunkLine = createTurtle([x, 0 + noise(i) * 0.3]);
```



Bump up the number of lines and that's our trunk!



## the leaves

Now let's draw those leaves. This is going to be a random walk through a perturbed signed distance field for a circle.



We'll start with a random walk.

```js
const randomWalk = createTurtle();

const step = 0.05;
for (let i = 0; i < 1000; i++) {
  let angle = randInRange(-1, 1) * 17;
  randomWalk.right(angle);
  randomWalk.forward(step);

  const [endX, endY] = randomWalk.end;
}

drawTurtles([ randomWalk ]);
```



We want this walk to stay in a circle though. What we'll do is define an equation for the distance from some circle. If we step outside (the distance becomes positive) then take a step back towards the circle. Signed distance fields are very powerful tools, which are rewardingly worth exploring.

```js
let startPt = [0, 0];

const r = 2;
const sdf = (x, y) => circleSDF([x, y], startPt, r); // using our circle SDF as a helper function

const randomWalk = createTurtle(startPt);

const step = 0.05;
for (let i = 0; i < 1000; i++) {
  let angle = randInRange(-1, 1) * 17;
  randomWalk.right(angle);
  randomWalk.forward(step);

  const [endX, endY] = randomWalk.end;
  const distance = sdf(endX, endY); // how far are we from the circle
  if (distance > 0) {
    // are we outside
    const up = sdf(endX, endY + step);
    const down = sdf(endX, endY - step);
    const right = sdf(endX + step, endY);
    const left = sdf(endX - step, endY);
    const gradX = (right - left) / (2 * step);
    const gradY = (up - down) / (2 * step);

    let a = (Math.atan2(gradY, gradX) / Math.PI) * 180;
    a += randInRange(-1, 1) * 102;
    a += 180;
    randomWalk.setAngle(a);
    randomWalk.forward(step);
  }
}

function circleSDF([x, y], start, r) {
  let dx = x;
  let dy = y;

  dx -= start[0];
  dy -= start[1];

  return Math.sqrt(dx * dx + dy * dy) - r;
}
```



Break up the lines to make them look like abstract scribbles.

```js
const step = 0.05;
for (let i = 0; i < 10000; i++) {
  let angle = randInRange(-1, 1) * 17;
  randomWalk.right(angle);
  randomWalk.forward(step);

  const [endX, endY] = randomWalk.end;
  const distance = sdf(endX, endY); // how far are we from the circle
  if (distance > 0) {
    // are we outside
    const up = sdf(endX, endY + step);
    const down = sdf(endX, endY - step);
    const right = sdf(endX + step, endY);
    const left = sdf(endX - step, endY);
    const gradX = (right - left) / (2 * step);
    const gradY = (up - down) / (2 * step);

    let a = (Math.atan2(gradY, gradX) / Math.PI) * 180;
    a += randInRange(-1, 1) * 101; // try adjusting this direction scale
    a += 180;
    randomWalk.setAngle(a);
    randomWalk.forward(step);
  }

  if (rand() < 0.59) {
    randomWalk.up();
  } else {
    randomWalk.down();
  }
}
```



Now we can shape the circle by scaling it and adding noise.

```js
function circleSDF([x, y], start, r) {
  let dx = 0.57 * x;
  let dy = 0.48 * y;

  dx -= start[0];
  dy -= start[1];

  return (
    Math.sqrt(dx * dx + dy * dy) -
    r +
    noise([x, y], { octaves: 1 }) * 1.1 +
    noise([x * 0.01, y * 0.01], { octaves: 1 }) * 0.53
  );
}
```



Let's add a little noise to the shading too.

```js
if (rand() < +0.6 + noise([endX * 18.7, endY * 1.34]) / 1.8) {
  randomWalk.up();
} else {
  randomWalk.down();
}
```



Now let's bump down the step and up the iteration count and we get something like this. Here are a few parameters and approximately what they were adjusted to.

```js
let step = 0.03;

i < 100000;

const r = randInRange(0.4, 2.1);
```



We can put this together with the trunk with some minor adjustments.

```js
let startPt = trunk.ct;

randomWalk.rotate(randInRange(-5, 5)).translate([-0.1, -0.6]);

drawTurtles([ randomWalk, trunk ]);
```



And that's our tree!

There is much to discover playing around in the parameter space. Some come out looking quite realistic.



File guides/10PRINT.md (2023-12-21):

---
title: 10PRINT
thumbnail: https://cloud-ajv6et0c3-hack-club-bot.vercel.app/0the_ppg256_article_image.webp
contributors: henrybass
---

## Beginner, 25min

_This tutorial is aimed at beginners, but it works best if you have a little prior programming experience._

"10PRINT" is one of the oldest and most well-known examples of generative art. It was originally created for the Commodore 64 in BASIC, and the code looked like this:
`10 PRINT CHR$(205.5+RND(1)); : GOTO 10`
From just that one line, the following intricate pattern is created:

10print

There's even a book named after this program: [10print.org](https://10print.org/)! For this guide, let's try to replicate this artwork for **_Blot_**. (This tutorial works fine if you don't have one!)

A Blot is a small drawing robot that can be programed from a browser. You send it instructions through code, and it follows those instructions to create a drawing. By the end of this guide, you will have created some art that can be drawn by the machine!





Here are some examples of art people have made with Blot:







Now, let's take another look at the original 10PRINT artwork that we'll try to replicate.



The artwork seems to be a grid of slashes. Some slashes point to to the top-right, others point to the bottom-right. Overall, the distribution seems to be about 50/50. If you look closely, you might notice that the slashes are just plain text: "/" or "\\". In fact, the Commodore program just prints a random sequence of characters to the screen, left to right. The challenge is, in the Haxidraw editor, you can't write symbols directly to the screen - we'll have to draw the slashes as lines.

On a high level, here's our strategy:

- Like a typewriter, move horizontally, drawing a forwards or backwards slash at each square randomly. Once we hit the end of a row, return to the start.

This looks like:



So, let's start making something! Boot up the editor at [editor.haxidraw.hackclub.com](https://editor.haxidraw.hackclub.com/). On the left side of the screen, you write code. On the other side, you can see a preview of what you're building. At any point, press "**Run Code**" at the top to see what you've made so far.

Let's start by defining a constant `t`: this will represent our turtle. The turtle is basically our pen - we can send it instructions like `t.up()` or `t.goTo([x,y])` to move it around. For example, calling `t.down()` places the pen on the paper, and `t.goTo([0, 0])` moves the pen to the position `0, 0`.

```
const t = new Turtle();
```

Directly below that, write `drawTurtles(t);`. This function makes it so that we can see the turtle's path in the preview window as we add to it.

Now, we can declare two more constants, to represent the size and spacing of our grid. It'll be useful to have these things as constants, because then we can easily change them later in the code to tweak the final image. The `gridSpacing` constant just dictates how far apart each slash of our drawing should be. A lower `gridSpacing` value means the pattern is more detailed, but you can change this value to whatever you want. The `gridSize` represents how large the final image should be.

```
const gridSize = 10;
const gridSpacing = 0.5;
```

Now, we can get to building up the artwork. To be able to draw each line, we can create a `draw` function. This is a block of code that takes in 4 parameters: The x and y position to draw to, along with the width and height of the slash we're going to draw.

```
function draw(x, y, width, height) {
```

First, randomly choose whether to draw a forwards or backwards slash. This can be done in code by calling `rand()` - a function that returns a random number between 0 and 1. If it's greater than 0.5, (this will be true 50% of the time), we draw a backslash.

```
  if(Math.random() >= 0.5) {
```

To actually draw the slash, we need to give the turtle a few instructions. Start by raising the pen with `t.up()`, then go to our start position at `x, y`. Lower the pen, and move to the bottom-right a little bit, by adding `width` and `height` to the turtle position.

```
    t.up();
    t.goTo([x, y]);
    t.down();
    t.goTo([x + width, y + height]);
```

If the random number was instead below 0.5, then we can draw a forward slash. This is done in an `else` statement:

```
  } else {
```

Raise the pen, but this time, start out a bit to the right of `x, y`. Lower the pen, and then move down by `height` from `x, y`. That's a forward slash!

```
    t.up();
    t.goTo([x + width, y]);
    t.down();
    t.goTo([x, y + height]);
  }
}
```

Visually, this looks like:



We've finished the drawing function, but we still need to call it. To run some code repeatedly, we use a `for` loop. We move across each row, left to right. At each grid cell, we call the `draw` function to draw the random slash. Once we hit the end of a row, we return to the start.

If you need a refresher on how for loops work, the syntax is like this:

```
for (code to run at the start of the loop;
	keep looping as long as this code is true;
	do this every loop) {
	run this code every loop;
}
```

We'll want to loop through every row in the grid. By setting `y` to negative `gridSize`, we effectively shift the whole image down the screen. We do this to ensure that it's within range for the Haxidraw to draw. To move to the next row, we add `gridSpacing` to `y` every time we loop. We only break once `y` reaches zero, because that means it's traveled a total distance of `gridSize`, and we've drawn the image.

```
for (let y = -gridSize; y < 0; y += gridSpacing) {
```

Each time we're at a new row, start moving horizontally by increasing `x`. At every `x` position draw a slash there by calling our `draw` function at that point.

```
  for (let x = 0; x < gridSize; x += gridSpacing) {
    draw(x, y, gridSpacing, gridSpacing);
  }
}
```

And, lastly, let's draw this to the screen! This is done simply by calling the function `drawTurtles` with the turtle we defined at the start.

`drawTurtles([ t ]);`

And, you're done! If all went well, you should be seeing something like the below art:



Great job! You can still go farther with this, if you want.

- See what happens if you change the probability in our `draw` function from `0.5` to something else
- Try changing how detailed the artwork is, by tweaking `gridSpacing`
- See what other patterns emerge when you draw things other than slashes

Also - if you have a Haxidraw on hand, go through [this guide](https://haxidraw.hackclub.com/) for instructions on how to set it up. After that, press "run machine", and watch the Haxidraw draw the art you created!

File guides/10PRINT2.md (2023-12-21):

---
title: 10PRINT2
thumbnail: https://cloud-ajv6et0c3-hack-club-bot.vercel.app/0the_ppg256_article_image.webp
contributors: henrybass
---

_This tutorial is aimed at beginners, but it works best if you have a little prior programming experience._

"10PRINT" is one of the oldest and most well-known examples of generative art. It was originally created for the Commodore 64 in BASIC, and the code looked like this:

```basic
10 PRINT CHR$(205.5+RND(1)); : GOTO 10
```

From just that one line, the following intricate pattern is be created:

10print2

There's even a book named after this program: [10print.org](https://10print.org/)! For this guide, let's try to replicate this artwork for **_Blot_**. (This tutorial works fine if you don't have one!)

A Blot is a small drawing robot that can be programed from a browser. You send it instructions through code, and it follows those instructions to create a drawing. By the end of this guide, you will have created some art that can be drawn by the machine!





Here are some examples of art people have made with Blot:







The artwork seems to be a grid of slashes. Some slashes point to to the top-right, others point to the bottom-right. Overall, the distribution seems to be about 50/50. If you look closely, you might notice that the slashes are just plain text: "/" or "\\". In fact, the Commodore program just prints a random sequence of characters to the screen, left to right. The challenge is, in the Haxidraw editor, you can't write symbols directly to the screen - we'll have to draw the slashes as lines.

Let's start by defining a constant `t`: this will represent our turtle. The turtle is basically our pen - we can send it instructions like `t.up()` or `t.goTo([x,y])` to move it around. For example, calling `t.down()` places the pen on the paper, and `t.goTo([0, 0])` moves the pen to the position `0, 0`.

```js
const t = createTurtle()
```

Directly below that, write `drawTurtles([ t ]);`. This function makes it so that we can see the turtle's path in the preview window as we add to it.

Since the original artwork is made up of many diagonal lines, we'll need a function that can draw these.

```js
function drawSlash(x, y, width, height) {
  t.up()
  t.goTo([x, y])
  t.down()
  t.goTo([x + width, y + height])
}
```

When we call this function, you should see a small slash in a corner of the screen.

```
drawSlash(0, 0, 10, 10);
```



We can draw more by using a `for` loop.

```js
for (let i = 0; i < 10; i++) {
  drawSlash(0, 0, 12, 12)
}
```

You'll still only see one, because they all overlap. We can draw more by moving the slash to the right each time we loop.

```js
drawSlash(0 + i, 0, 12, 12)
```



That's a start, but they're too close together. We want them to be evenly spaced out in a grid.

```js
const gridCellSize = 12
for (let i = 0; i < 10; i++) {
  drawSlash(i * gridCellSize, 0, 12, 12)
}
```



Now, let's do the same, but on the `y` axis.

```js
const gridCellSize = 12
for (let i = 0; i < 10; i++) {
  for (let j = 0; j < 10; j++) {
    drawSlash(i * gridCellSize, j * gridCellSize, gridCellSize, gridCellSize)
  }
}
```



The lines don't quite reach the edge of the screen, though. Try changing `gridCellSize` until it fits.



We're getting close, but all the lines still face in the same direction. Going back to `drawSlash`, try flipping the lines we draw horizontally, making them face the other way.



In the original 10PRINT artwork, the lines can face in either direction randomly. By calling the `rand()` function built into Haxidraw, we can randomly swap between the two line styles.

Since `rand()` returns a number between 0 and 1, 50% of the time it's going to be over 0.5.

```js
function drawSlash(x, y, width, height) {
  if (rand() > 0.5) {
    t.up()
    t.goTo([x + width, y])
    t.down()
    t.goTo([x, y + height])
  } else {
    t.up()
    t.goTo([x, y])
    t.down()
    t.goTo([x + width, y + height])
  }
}
```

Good work!



If we change 0.5 to something lower, we see more of one type of line than another.



# Further experimentation

- Try making the grid more dense, while keeping it the same size on the screen
- Change the line to something else

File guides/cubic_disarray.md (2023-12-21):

---
title: Cubic Disarray
thumbnail: https://cloud-r9jbhouts-hack-club-bot.vercel.app/0im.webp
contributors: henrybass
---

**_Georg Nees_** was a pioneer of digital art, responsible for interesting works like Cubic Disarray.

cubic disarray

Let's try to recreate this in the Blot editor. A good first step to reverse engineering any artwork is to break it down into the obvious components. There's a grid of squares, and the squares closer to the bottom seem to be rotated more and more.

We can get started by setting up a turtle, and define some constants:

```js
const t = createTurtle()

const size = 10
const squareSize = 1

// ... other code goes here ...

drawTurtles([ t ])
```

Obviously we'll need a way to draw these rotated squares, so let's define a function for that:

```js
function draw(x, y, width, height, theta) {
  t.up()
  let startX = x - height / 2
  let startY = y - height / 2

  t.goTo(rotatePoints(x, y, startX, startY, theta))
  t.down()
  t.goTo(rotatePoints(x, y, startX + width, startY, theta))
  t.goTo(rotatePoints(x, y, startX + width, startY + height, theta))
  t.goTo(rotatePoints(x, y, startX, startY + height, theta))
  t.goTo(rotatePoints(x, y, startX, startY, theta))
  t.up()
}
```

This function takes in a `x`, `y` position, along with a `width` and `height` for the square. Lastly, we'll want a `theta` to rotate the points by. The function works by creating a square path, and rotating it around the center by a given amount. We still need to define how to do this rotation, though.

This can be done using the sine and cosine functions. They decompose a given angle into an x and y component, which we can use to preform the rotation. The function takes in:

- An origin x and y to rotate around
- The x and y to rotate
- The angle to rotate by

It then returns the rotated points as an array.

```js
function rotatePoints(ox, oy, x, y, theta) {
  let dx = x - ox
  let dy = y - oy
  let newX = dx * Math.cos(theta) - dy * Math.sin(theta)
  let newY = dx * Math.sin(theta) + dy * Math.cos(theta)
  return [newX + ox, newY + oy]
}
```

Great, we're almost done! Now it's down to simply drawing the grid. Loop over every x and y in some range, and draw a square there. We rotate them by a random amount, scaled proportional to how low the square is on the screen.

```js
for (let x = 0; x < size; x++) {
  for (let y = 0; y < size; y++) {
    draw(x, y, squareSize, squareSize, (Math.random() - 0.5) * ((10 - y) / 10))
  }
}
```

And, you're done! The final result should look something like this in the editor:



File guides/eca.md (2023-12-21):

---
title: Elementary Cellular Automata
thumbnail: https://cloud-i7potzeq3-hack-club-bot.vercel.app/00image-2-2.webp
contributors: henrybass
---

### (Henry Bass, Beginner/Intermediate, 20min)

[Elementary Cellular Automata](https://en.wikipedia.org/wiki/Elementary_cellular_automaton) is one of the simplest classes of [Cellular Automata](https://en.wikipedia.org/wiki/Cellular_automaton).

Through extremely simple rules, complex patterns can be created.

elementary cellular automata
elementary cellular automata

The rules behind Elementary Cellular Automata, or ECA, are very simple.

First, set up a strip of cells, with each one having a state of either one or zero. This is the first generation. Then, start iterating through the next generation. Depending on the 3 cells above, we either set this new cell as alive or dead. This is best explained in the gif below:



The rules for when to set the new cell as a one or a zero are specified by a rule code. For example, here's how to interpret rule 30:

First, convert 30 into binary digits:
**00011110**

Each of these digits correspond to some possible state the previous that the 3 above cells can be in. For example:

**digit: 0** Since this digit is a 0, whenever the above 3 digits are [0, 0, 0] (_zero in binary_), the below cell in the next generation should be a 0

**digit: 4** Since this digit is a 1, whenever the above 3 digits are [1, 0, 0] (_four in binary_), the below cell in the next generation should be 1

**digit 7: 1** Since this digit is a 0, whenever the above 3 digits are [1, 1, 0] (_seven in binary_), the below cell in the next generation should be 0

Remember, we start counting from zero in this case, not one.

### Starting the code

Create a turtle:
`const t = new Turtle()`

Define the first generation, and fill it randomly:

```
const width = 50
let genStart = Array(width).fill(0)
genStart = genStart.map(() => (Math.round(Math.random())))
```

You might have noticed that there are several conversions between binary and decimal in the ECA algorithm we defined. It'll help to create a function that can do this for us:

```
function toBits(num, overhead) {
  let bits = num.toString(2)
  return (("0".repeat(overhead - (bits.length))) + bits).split("").map((s) => {return parseInt(s)})
}
```

The function first converts the integer into a binary string with `toString(2)`. We then add an overhead, and convert this into an integer array.

Here's what overhead does:

- Without overhead: `toBits(1) -> 1`
- With overhead: `toBits(1, 8) -> 00000001`

This helps because we often care about the full bit sequence, not just the direct binary conversion.

Next, let's define a rule string, and convert it to an 8 bit sequence:
`let rule = toBits(54, 8)` (Rule 54)

Then, we can create an array for the generation history, starting with `genStart`:
`let allGens = [genStart]`

Great! Now, it's time to define how new generations are created.

```
function nextGen(prev) {
  let nextGen = []
```

Iterate through the previous generation:

```
  for (let i = 0; i < prev.length; i++) {
```

Check what state it's in:

```
    for (let state = 0; state < 8; state++) {
      bits = toBits(state, 3)
```

We then check if the state matches, and if it does, follow the rule defined:

```
      let left = (i <= 1) ? 0 : prev[i - 1]
      let center = prev[i]
      let right = (i >= (prev.length - 1)) ? 0 : prev[i + 1]
      if (left == bits[0] && center == bits[1] && right == bits[2]) {
        nextGen.push(rule[8 - state - 1])
        break
      }
    }
  }
  return nextGen
}
```

Now, how should we draw this?
Since the Blot can't directly render pixels, we'll have to be a _bit_ more creative with how we do this.

By using the following rendering method, we can some visually interesting results:

- For each pixel rendered, check the 3 pixels above
- Draw a line to any above pixel if it's filled



Here's that in code:

```
function drawGen(arr, gen) {
  prevGen = allGens[gen]
```

`y` is negative because we're drawing top to bottom:

```
  let y = -gen
  for (let x = 0; x < arr.length; x++) {
```

If there's a 1 at this position, do the drawing procedure:

```
    if (arr[x]) {
      t.up()
      t.goTo([x, y])
      t.down()
```

Check the 3 above cells, and if they're in the 1 state, draw a line to them:

```
      if (prevGen[x] == 1) t.goTo([x, y + 1])
      t.goTo([x, y])
      if (prevGen[x - 1] == 1) t.goTo([x - 1, y + 1])
      t.goTo([x, y])
      if (prevGen[x + 1] == 1) t.goTo([x + 1, y + 1])
      t.goTo([x, y])
      if (arr[x - 1] == 1) t.goTo([x - 1, y])
      t.goTo([x, y])
    }

  }
  t.up()
  t.goTo([w, -y - 1])
}
```

Finally, iterate through the generations, and draw:

```
for (let gen = 0; gen < w; gen++) {
  allGens.push(nextGen(allGens[gen]))
  drawGen(allGens[gen + 1], gen)
}

drawTurtles([ t ])
```

Great job! There are plenty of variations on ECAs that you can explore. Here's a few more drawings done with the code, by setting only the center pixel as a one:





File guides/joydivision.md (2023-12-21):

---
title: Joy Division
thumbnail: https://external-content.duckduckgo.com/iu/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
contributors: henrybass
---

Here's the cover to Joy Division's first album. The actual album is based on [real data](https://blogs.scientificamerican.com/sa-visual/pop-culture-pulsar-origin-story-of-joy-division-s-unknown-pleasures-album-cover-video/), but we'll try to make a simpler version.



First, let's start by noticing what we see in the image. It seems to be composed of several horizontal lines, each vertically distorted randomly. More specifically, the distortion closer to the center is more extreme, while it's flattened farther out. There's also another, smaller amount of random distortion evenly distributed across each line.

Let's give this a shot! First, simply declare a turtle, and draw it's path to the screen:

```js
const t = new Turtle();
drawTurtles([ t ]);
```

To actually get it to draw something, we can iterate through a grid, drawing horizontal lines:

```js
const height = 13;
const lineWidth = 10;
const lineSpacing = 0.2;
const dx = 0.005;

for (let line = 0; line < height; line += lineSpacing) {
  for (let x = -lineWidth/2; x < lineWidth/2; x += dx) {
    let height = line;
    if (x == -lineWidth/2) t.up();
    t.goTo(
      [x, height]
    );
    t.down();
  }
}
```

Each line is spaced vertically by `lineSpacing`, and composed of many line segments, each with length `dx`. We lift the turtle with `t.up()` at the start of each line to break up the path into horizontal strips.

You should now be seeing a bunch of straight horizontal lines. Let's add some randomness!

A first attempt may look something like this:

```js
let height = Math.random();
```

You'll quickly notice that this doesn't look too good - the offset is _too_ random. A good compromise is smooth noise. This kind of noise is random on large scales, but smooth when looked at close up. It's good for natural-looking curves, and matches the randomness seen on the Joy Division album cover.

We can call this in the Blot editor with `noise([x, y], {octaves:n, falloff:k})`. The octaves dictate how intricate this noise is, and the falloff dictates how much the small scale detail should affect the final value.

We don't want pure smooth noise, and we'll instead want to modify how we sample it a bit. Set `height` equal to `line + sampleNoise(x, line)`, and define that function:

```js
const baseNoiseHorizontalScale = 1.5;
const baseNoiseVerticalScale = 10;
const baseNoiseAmp = 0.1;

const addedNoiseScale = 3.2;
const addedNoiseAmp = 0.2;

function sampleNoise(x, y) {
  let baseNoise = (
	  baseNoiseAmp *
	  Math.pow(distFromCenter(x), 2) *
	  noise([x * baseNoiseHorizontalScale + 14, y * baseNoiseVerticalScale], {octaves:2})
  );
  let addedNoise = addedNoiseAmp * noise([x * addedNoiseScale - 17, y], {octaves:2})
  return baseNoise + addedNoise
}
```

This function takes in a x and y, and returns some modified noise at that position. We can break the noise seen in the album cover down into 2 layers:

- Base noise: This is stronger when closer to the center, and weaker farther way. It appears to be quite smooth
- Added noise: This is more random, and distributed evenly across the whole image

We define a few constants to dictate how vertically and horizontally stretched both layers of noise should be, along with a final amplitude.

Notice that when defining the base noise, we use a function `distFromCenter`. We'll have to define this as such:

```js
function distFromCenter(x) {
  return lineWidth/2 - Math.abs(x)
}
```

When incorporating this distance into the base noise, we also square the value. This simply leads to a slightly nicer looking height distribution.

This looks close to the final product, but there's still one big thing that it's missing. Lines can overlap with each other, which really doesn't make sense. What we need is _occlusion_. This means that lines closer to the front of the screen hide lines behind them. There's a quick and hacky way to do this:

- Store an array corresponding to the maximum height so far in each vertical column
- Only draw a line when it's higher than the previous max height
- If it's the new highest, set corresponding point in the array to it's height

Create the array, and fill it with zeroes:

```js
let maxHeights = new Array(lineWidth / dx);
```

Above the line `if (x == -lineWidth/2) t.up();` in our main loop, add the following logic doing what we outlined earlier:

```js
    let maxHeightsIndex = Math.floor((x + lineWidth/2) / dx)
   if (height > maxHeights[maxHeightsIndex]) {
      t.down()
      maxHeights[maxHeightsIndex] = height
    } else {
      t.up()
    }
```

The occlusion works best when `dx` is really low.

And that's it, you're done! When drawing the final image, you should see something like this:



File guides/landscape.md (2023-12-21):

---
title: Landscape
thumbnail: https://cloud-bxuqstv0l-hack-club-bot.vercel.app/00image-2.webp
contributors: henrybass
---

### (Intermediate, ~45 min, by Henry Bass)

landscape

This is an explainer on how to create art like the image above in the [Blot editor](https://blot.hackclub.dev/). It assumes some knowledge of programming in JavaScript and how Blot works, but nothing beyond that.

#### Steps:

- Create a height-map
- Draw it
- Add occlusion
- Make it look nice

## Creating a height-map

To try and create realistic terrain, we should first look at the real thing. Here's a map of some hills in Canada:


Notice that, although the terrain is complex, it looks somewhat random. There's also seemingly random detail at both large and small scales, from massive hills to small bumps.

To replicate this in code, a technique is used called Fractal Noise. A reasonable first step would be to start out with pure randomness.

Here's an image made up of large pixels of completely random brightness:



Real terrain, of course, isn't made up of large squares. To get closer to the real thing, we can blur this image to make it smoother.



This is much closer, but it's missing an essential aspect: Detail. Hills on a large scale resemble our image, but that resemblance breaks when we look closer. Conveniently though, the detail at both large and small scales looks pretty similar. So to capture this, we can try adding together our random noise on different scales. Each time, we decrease the amplitude of the noise and the blur radius ("Sigma"), while increasing the frequency.



That looks a lot closer! As a note, the amount we change the frequency, amplitude, and blur with respect to each octave is arbitrary, and tweaking those functions can lead to interesting variations of our noise. The name of this technique is: _Fractal Noise_.

In fact, the Blot editor actually has a function for fractal noise built in!

```js
// y and z are optional
noise(
  [
    x: number,
    y: number,
    z: number
  ],
  {
    octaves = 4,
    falloff = 0.5
  }
)
```

We can sample a fractal noise function at any x and y by calling `noise([x, y])`. By default, this calculates fractal noise with 4 octaves and a 50% decrease in amplitude for each, but you can change this as needed. Now that we have the function, let's turn this into height.

## Drawing the noise

First, we can initialize a new Turtle with `const t = new Turtle()`.

Then, iterate over all the points within some area, such as 0 < y < 15 and 0 < x < 10, moving by a small value `dx` and `dy` each time.

```js
const dx = Some small number
const dy = Vertical spacing between lines
const noise_x_scale = How horizontally stretched the noise is
const noise_y_scale = How vertically stretched the noise is
const noise_amp = The height scale of the terrain

function getHeight(x, y) {
	return noise(
	[x * noise_x_scale, y * noise_y_scale]
	) * noise_amp
}

for (let y = 0; y < 15; y += dy) {
	for (let x = 0; x < 10; x += dx) {
		height = getHeight(x, y)
	 }
}
```

Using the `t.goTo([x, y])` function in Blot, we can create straight lines. If we want to replicate a smooth curve, we have to use many `goTo` commands with very small changes in the x and y.

If we just call `t.goTo([x, y])` at every x and y in our loop, we'll get straight lines. Instead, let's add the noise height to this, with `t.goTo([x, y + height])`.

Using `drawTurtles(t)` at the end, we can visualize the path.
You may notice that there's a straight line between the start and end of each path. This is because the pen is still down when we start a new line, and it can be solved by simply raising the pen if we're going to the first point of a new line.

If all goes well, you should see many rough lines, that look something like this:



To give the appearance that we're looking at this from the side, we can divide the y value by 2 or 3 in each `goTo` command. This will shrink the terrain vertically, but leave the hill height the same.

This is starting to look like mountains! If we want to make these look more like islands instead, we'd need to cut off the noise below a given height, and replace it with flat-looking water. By returning `Math.max(height, sea_level)` in our `getHeight` function, only the larger of the two values will be returned. This means we'll see a line at sea level whenever the noise height is below it.

That water still looks a bit boring, though! Trigonometric functions like `Math.sin()` and `Math.cos()` are great for creating wave-like patterns. If we add the sine of the x value to the sea level, the water will be higher and lower in a wave-like pattern. Going further, by offsetting the input to the sine function by another wave, such as the cosine of the y value, the waves will sway side to side depending on how far up in the image they are. If you're not following along with why this works, try tweaking constants and scaling the waves in various ways to gain an intuition for what each part of the code contributes to the output.

```js
sea_level =
  default_wave_height +
  wave_height * Math.sin((x + Math.cos(y * offset_freq)) * wave_freq)
```

Of course, for this code, you'd need to set actual values to all the variables mentioned. By now, you'll probably have something that looks like this:



Most of the hard work is done by now! But, you might be noticing a big problem with how this all looks, especially with high enough mountains. We can see through the terrain in some places! Because we're just 2D drawing lines that _look_ 3D, paths in "front" of others won't block paths that are "behind". To solve this, we need something called **occlusion**.

## Adding occlusion

Occlusion can be tricky, so it'll help to break down the problem a bit.

Our problem:

> If an line is in **front** of another, and the other line goes **under** it, it should be **invisible**

Let's define some of those phrases in the context of our code:

> **Front**: Lines that we draw earlier in our loop along the y axis are the ones that should be occluding others
> **Under**: If a line has the same x value as another but a lower y value, it's under it
> **Invisible**: We should raise the pen before moving to it

So, we need to remember where the previous lines in the same x column are, to check if our current line is in front. Actually, we only need to store the maximum y value in our column, because there's no need to occlude behind a line when there's another higher one.

We can store these values simply using an array where each index corresponds to some x value we'll stop at:
`let maxHeights = Array(Math.floor(screen_width/dx)).fill(0)`

Now, for each point, we can check if we're below the previous maximum y value, with `if (height + y/3 > maxHeights[Math.floor(x/dx)])`. If so, simply set our current height to be the new maximum at this `maxHeights` index, and draw. Otherwise, raise the pen.

`dx` has to be lowered a lot after this, because otherwise there's a lot of obvious artifacts.

Once that's implemented, the image will look more like this:



If you compare that to the image before occlusion, you'll see the difference. Now, we're almost done! The image still looks a bit too much like just noise, and we can go farther to make it look like real islands.

## Making it look nice

An easy fix would be to add some perspective. This can be done by shrinking hills proportionally to their distance. Simply divide the height by y plus some number: `(y + perspective_offset)` at the end of the `getHeight` function. We need to add that extra value to y because 1/x is asymptotic at 0, and we want to avoid the infinity. In 3D, you can think of this as moving backward some distance from the first hill. This change will probably have to be counteracted by changing the sea level and default hill height, because we're shrinking distant hills so much.

We're really close to a complete image, but there's a one more thing we can add to really make the image look nicer: trees.

Trees generally grow a good distance above sea level, and they're pretty random in height. Luckily for us, trees can be easily approximated as straight lines from far enough away. Simply create a `drawTree(x, y)` function, that creates a vertical line like this:

```js
size = tree_size * Math.random() + size / 2
t.goTo([x, y])
t.goTo([x, y + size])
t.up()
t.goTo([x, y])
```

Then, we should only call this if `Math.random() > tree_prob && height * (y + perspective_offset) > tree_line`. We multiply by `(y + perspective_offset)` to cancel out the division back in the `getHeight` function, and ignore perspective. With all this done, you'll have a nice looking landscape, generated 100% from code. Great job!



## More experimentation

- Try tweaking all the parameters, and see if you can create different types of environments.
- What happens if we use a different noise function?
- The way we implemented perspective only shrinks distant hills vertically. See what happens if you decrease the horizontal noise scale as the hills get farther away, and try using that for more realistic perspective.
- Add more decorations! We've added trees, but you could also add houses, rocks, or anything.

## The code

I've avoided giving away too much code, as it's more fun to work through some of the potential problems yourself, but if you get stuck somewhere along the guide, you can reference this:

```js
const t = new Turtle()

const dx = 0.005
const dy = 0.26
const noise_x_scale = 0.4
const noise_y_scale = 0.6
const noise_amp = 28.2

const wave_height = 0.052
const offset_freq = -1.3
const wave_freq = 16.5
const default_wave_height = 11
const tree_size = 0.04

let maxHeights = Array(Math.floor(10 / dx)).fill(0)

function drawTree(x, y) {
  size = tree_size * Math.random() + size / 2
  t.goTo([x, y])
  t.goTo([x, y + size])
  t.up()
  t.goTo([x, y])
}

function getHeight(x, y) {
  let height = noise([x * noise_x_scale, y * noise_y_scale]) * noise_amp
  sea_level =
    default_wave_height +
    wave_height * Math.sin((x + Math.cos(y * offset_freq)) * wave_freq)
  return Math.max(sea_level, height) * (1 / (y + 10))
}

for (let y = 0; y < 15; y += dy) {
  for (let x = 0; x < +6; x += dx) {
    height = getHeight(x, y)
    if (height + y / 3 > maxHeights[Math.floor(x / dx)]) {
      maxHeights[Math.floor(x / dx)] = height + y / 3
      if (x == 0) {
        t.up()
      } else {
        t.down()
      }
      if (Math.random() > 0.75 && height * (y + 9) > +13.0) {
        drawTree(x, y / 3 + height)
      }
    } else {
      t.up()
    }
    t.goTo([x, y / 3 + height])
  }
}

drawTurtles([ t ])
```

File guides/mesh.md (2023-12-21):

---
title: Draw a triangle mesh
thumbnail: https://cloud-mgfukhxlr-hack-club-bot.vercel.app/00image__1_.webp
contributors: henrybass
---

### This guide is based on a tutorial on _[generativeartistry](https://generativeartistry.com/tutorials/triangular-mesh/)_ by [maxwellito](https://maxwellito.com/)

---

triangle mesh

We'll build the above mesh like this:

- First, generate a grid of points, where every other line is slightly offset
- Next, offset each point according to some noise
- Then, we iterate through that grid, drawing triangles at every 3 points

### Let's start with some code

First, create a turtle:
`const t = new Turtle();`

Next, let's define a scale for the whole image:
`const size = 80`

Then, we can create a grid. This is identical to a typical rectangular grid, except we offset every other line by a bit, making it triangular.

```js
var line, dot,
    odd = false,
    lines = [],
    gap = 1;

for(var y = gap / 2; y <= size; y+= gap) {
  odd = !odd;
  line = [];
  for(var x = gap / 4; x <= size; x+= gap) {
    dot = {x: x + (odd ? gap/2 : 0), y: y};
```

Then, use the built-in blot noise function to offset the points again, this time randomly. Also, add an offset on the x axis if we're drawing an odd-numbered line.

```js
    let n = noise([x * 0.1, y * 0.1])
    line.push({
      x: x + (n*4.1 - .4) * gap  + (odd ? gap/2 : 0),
      y: y + (n*6.9 - .4) * gap
    });
  }
  lines.push(line);
}
```

Now, we need a way to draw this. We can define a simple function to render a triange, where we simply go through every point of the triangle with the turtle `goTo` function.

```js
function drawTriangle(pointA, pointB, pointC) {
  t.goTo([pointA.x, pointA.y]);
  t.down()
  t.goTo([pointB.x, pointB.y]);
  t.goTo([pointC.x, pointC.y]);
  t.goTo([pointA.x, pointA.y]);
  t.up()
}
```

Now, to draw the whole mesh, we can iterate through the points, drawing triangles at every 3 points next to each other in 2D.

```js
var dotLine;
odd = true;

for(var y = 0; y < lines.length - 1; y++) {
  odd = !odd;
  dotLine = [];
  for(var i = 0; i < lines[y].length; i++) {
    dotLine.push(odd ? lines[y][i]   : lines[y+1][i]);
    dotLine.push(odd ? lines[y+1][i] : lines[y][i]);
  }
  for(var i = 0; i < dotLine.length - 2; i++) {
    drawTriangle(dotLine[i], dotLine[i+1], dotLine[i+2]);
  }
}

drawTurtles([ t ])
```

And, that's it! If all went well, you should have an image resembling the one at the start of the guide.

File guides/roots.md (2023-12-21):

---
title: Roots
thumbnail: https://cloud-54f820d0z-hack-club-bot.vercel.app/00roots.webp
contributors: profsucrose
---

(Written by @profsucrose, if you have any issues or questions)

Let's walk through the process of how the following image was generated:

roots

## The first branch

We can first start by drawing a simple random walk, where during each step we (randomly) turn the turtle by a few degrees and then inch it forward. We'll later make this recursive, so let's put the logic in its own function `makeBranch`. The first branch will start at the center, so we also define the width and height of the document (in millimeters, as visualized as the blue rectangle) at the top as constants. We want the branch to start facing the bottom of the page, so we also rotate the turtle 90 degrees when creating it:

```js
const WIDTH = 10
const HEIGHT = 20

const t = createTurtle([WIDTH / 2, 0])
t.right(90)

const turtles = [t]

function makeBranch(turtle) {
  const n = 185

  for (let i = 0; i < n; i++) {
    const curl = randInRange(-5, 5)
    turtle.left(curl)
    turtle.forward(length)
  }

  return turtle
}

makeBranch(t)

drawTurtles([ turtles ])
```

You should get something like the screenshot below:



Let's then add width (or thickness) to the branch by, for each point, replacing it with two points separated by the path's normal vector at that point. As in, in `iteratePoints`, we get the angle (in radians) the turtle was facing at that point (`angleAtPoint`), and then get the corresponding left and right points by rotating left or right 90 degrees and stepping forward. By stepping we separate the center line into two as defined by the thickness value calculated in `thicknessAt`.

Let's put this logic in a new function, `thicken`, which takes in the branch's turtle and a thickness value, and the path accordingly. We then call this function at the end of `makeBranch`. The above edits are shown below (feel free to play around with the different constants!):

```js

function makeBranch(turtle) {
    ...

    thicken(turtle)

    return turtle;
}

function thicknessAt(t) {
  return 1-smoothstep(-1.3, 0.9, t)
}

function thicken(turtle) {
  const left = [];
  const right = [];

  turtle.iteratePath((pt, t) => {
    // getAngle() returns degrees, convert to radians
    const angleAtPoint = turtle.getAngle(t)/180 * Math.PI;

    const thickness = thicknessAt(t)

    const leftAngle = angleAtPoint - Math.PI/2
    const rightAngle = angleAtPoint + Math.PI/2

    const leftPoint = [
      pt[0] + thickness * Math.cos(leftAngle),
      pt[1] + thickness * Math.sin(leftAngle)
    ]

    const rightPoint = [
      pt[0] + thickness * Math.cos(rightAngle),
      pt[1] + thickness * Math.sin(rightAngle)
    ]

    left.push(leftPoint)
    right.push(rightPoint)
  })

  // Now, instead of drawing the center line, the turtle
  // consists of drawing just the left line and then the right.
  turtle.path = [left, right];
}

makeBranch(t, 0.1, 0)

drawTurtles([ t ])

// Smoothstep
function clamp(x, minVal, maxVal) {
  return Math.max(Math.min(x, maxVal), minVal)
}

function smoothstep(edge0, edge1, x) {
  const t = clamp((x - edge0) / (edge1 - edge0), 0.0, 1.0);
  return t * t * (3.0 - 2.0 * t);
}
```

For the easing function, we use a function called `smoothstep` (documented [here](https://registry.khronos.org/OpenGL-Refpages/gl4/html/smoothstep.xhtml)). If you're familiar with Bezier curves or easing functions, `smoothstep` is pretty similar: it takes in an `x` value (in this case time), left and right edges as x-values (`edge0`, `edge1`) and interpolates between the two through a smooth curve. This allows us to, in `thicknessAt`, have the returned thickness vary from `1` to `0` smoothly as `t` increases. `smoothstep` does not give you quite as much control as something like a Bezier curve, but for most easing tasks it works well enough and is easy to intuitively tweak via `edge0` and `edge1`.

If you're interested, here's a [visualization of smoothstep in Desmos](https://www.desmos.com/calculator/fyxbylpswj).

The above edits should produce something like:



## Reshaping the branch

Before we make more branches, let's change the random walk to make the "growth" behavior face down more (in a way crudely accounting for "gravity"). We can do this by, in each step, randomly sampling a target angle that the branch will try to curl towards to face. We'll then also need some logic for determining if the branch should turn clockwise or counterclockwise to get closer to the angle (a slightly harder problem than you may initially think).

Let's add this logic to `makeBranch`:

```js
// Mods angle to be from -180 - 180 degrees
function modAngleDeg(angle) {
  angle = Math.sign(angle) * (Math.abs(angle) % 360)
  if (angle > 180) return 180 - angle
  else return angle
}

function makeBranch(turtle, length, startingT) {
  const n = 185

  for (let i = 0; i < n; i++) {
    const time = i / (n - 1) // Scale i to be from 0-1. The "time" of the step
    const stdev = 200 // High standard deviation, we don't want the branch to be straight
    const average = -90 // Downwards
    const targetAngle = gaussianRandom(average, stdev) // Like Math.random(), but biased towards `average`

    const angle = turtle.angle // Current angle

    const moddedAngle = modAngleDeg(targetAngle) // Mod target angle to be from -180 - 180

    // moddedAngle and moddedAngle + 360 are equivalent; which
    // one is numerically closer determines which way to turn.
    const closerDiff = Math.min(moddedAngle - angle, moddedAngle + 360 - angle)
    const curl = closerDiff / 20 // Scale down

    turtle.left(curl)
    turtle.forward(length)
  }

  thicken(turtle, startingT)

  return turtle
}
```

To randomly sample an angle that is on average close to some "target" but can sometimes be far away, we can use the [normal/Gaussian distribution](https://en.wikipedia.org/wiki/Normal_distribution). We can then control how far each random angle can be from the target by changing the standard deviation (`stdev`) of the distribution. Math.random() in Javascript generates a number between 0 and 1 from a uniform distribution (any number is as likely as any other) so we can turn it into a normal distribution by doing a "Box-Muller transform." I.e., we can copy code from StackOverflow (I don't actually know statistics):

```js
// https://stackoverflow.com/questions/25582882/javascript-math-random-normal-distribution-gaussian-bell-curve
// Standard Normal variate using Box-Muller transform.
function gaussianRandom(mean = 0, stdev = 1) {
  const u = 1 - Math.random() // Converting [0,1) to (0,1]
  const v = Math.random()
  const z = Math.sqrt(-2.0 * Math.log(u)) * Math.cos(2.0 * Math.PI * v)
  // Transform to the desired mean and standard deviation:
  return z * stdev + mean
}
```

The shape of the branch should now be (subtly) different:



## Branches

We can add branches in `makeBranch` by, if the length of the current branch is long enough (twigs don't branch), creating some additional turtles which break off from the current branch:

```js
function makeBranch() {
    ...

    if (length > +0.05) {
        const nBranches = Math.floor(randInRange(1, 4)) // 1-3

        for (let i = 0; i < nBranches; i++) {
            const time = randInRange(0.02, 1);
            const pt = turtle.interpolate(time);
            const curAngleDeg = turtle.getAngle(time),
                curAngleRad = curAngleDeg/180 * Math.PI
            const parentThickness = thicknessAt(time + startingT)

            // Turn either left or right 90 degrees
            const a = (Math.random() > 0.5 ? 1 : -1) * 90

            // Move side branch out of parent
            pt[0] += parentThickness * Math.cos(curAngleRad - a)
            pt[1] += parentThickness * Math.sin(curAngleRad - a)

            const newBranch = new Turtle(pt);
            newBranch.setAngle(curAngleDeg);

            newBranch.right(a);
            makeBranch(newBranch, length*(1-time)*.90, time + startingT); // Recur

            turtles.push(newBranch) // Add to turtles array for drawing
        }
    }

    thicken(turtle, 0.8, startingT)

    return turtle;
}
```

This should produce something like:



# Texturing

Finally, let's add some texture by drawing rungs/"rings" throughout the path of each branch. Each ring consists of an initially straight line from `leftPoint` to `rightPoint`, where we then add noise to the line by adjusting individual points. We want the line to be more noisy towards the center and less so towards the ends, so we can again use `smoothstep`! This requires rewriting how `thicken` works, so the whole function with these edits made is shown below:

```js
function thicken(turtle, startingTime) {
  const nRings = 200
  const ringStepT = 1 / (nRings - 1)
  let nextRingT = ringStepT

  const left = []
  const right = []

  turtle.iteratePath((pt, t) => {
    /* Thicken line at point, as before */

    // getAngle() returns degrees, convert to radians
    const angleAtPoint = (turtle.getAngle(t) / 180) * Math.PI

    const thickness = thicknessAt(t, startingTime)

    const leftAngle = angleAtPoint - Math.PI / 2
    const rightAngle = angleAtPoint + Math.PI / 2

    const leftPoint = [
      pt[0] + thickness * Math.cos(leftAngle),
      pt[1] + thickness * Math.sin(leftAngle)
    ]

    const rightPoint = [
      pt[0] + thickness * Math.cos(rightAngle),
      pt[1] + thickness * Math.sin(rightAngle)
    ]

    left.push(leftPoint)
    right.push(rightPoint)

    /* But, every ringStepT, draw a ring from left to right */
    if (t >= nextRingT) {
      nextRingT += ringStepT

      /* Draw ring */
      // Start ring at leftPoint, draw straight line to rightPoint, then add noise

      const deltaX = rightPoint[0] - leftPoint[0]
      const deltaY = rightPoint[1] - leftPoint[1]

      const ring = new Turtle(leftPoint)
        .setAngle((Math.atan2(deltaY, deltaX) / Math.PI) * 180)
        .forward(Math.sqrt(deltaX * deltaX + deltaY * deltaY)) // Straight line from left to right
        .resample(0.01) // Resample so we can modulate individual points

      // Seed for noise
      const ringSeed = 1

      // Take normal vector of straight line by perpendicularizing the line (<x, y> -> <-y, x>)
      const normalMag = Math.sqrt(deltaX * deltaX + deltaY * deltaY)
      const normalX = -deltaY / normalMag
      const normalY = deltaX / normalMag

      // Add noise
      ring.iteratePath((ringPoint, ringT) => {
        const normal = ring.getNormal(ringT)

        // Smoothstep so more noisy in middle, less at edges
        const s =
          0.9 * smoothstep(-0.1, 0.4, 0.5 - Math.abs(ringT - 0.5)) * thickness
        const noiseMag = 2 * (noise([2 * ringT, ringSeed]) - 0.5) * s

        ringPoint[0] += normalX * noiseMag
        ringPoint[1] += normalY * noiseMag
      })

      turtles.push(ring)
    }
  })

  turtle.path = [left, right]
}
```

You should now be able to produce something like the screenshot below:



That's it! But you can still add a lot of features from here, if you're up to it:

- For instance, one thing to add would be occlusion, so each branch can be assigned a z-index and cover other ones, so many more branches can be rendered without being too busy
- Or, you could make the texturing more interesting by varying `ringSeed` for different branches or different regions
- You could render multiple initial branches/roots at the start, and generate random parameters for each one in an interesting pattern
- Add some logic so the branches stay within the blot bed/document always, and curl away from the edges if they get too close
- Generate a texture for the background

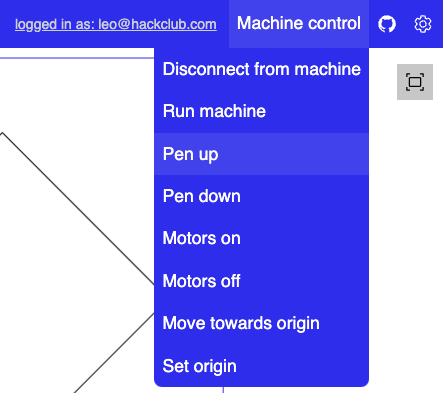
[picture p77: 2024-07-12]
docs/assembly/assets/Screenshot 2024-07-10 at 4.57.52 PM.png

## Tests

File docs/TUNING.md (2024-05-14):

# Using your blot

_Now that your blot is assembled, the next step is to set it up for your first drawing & tune it._

Start by moving the rails all the way to the right and forward, as shown below



Next, connect the power adapter to the port labeled "Usb Power", and connect your computer or laptop to the other port.
Connect the servo motor wires to the 3 pins as seen at the top of the image. The brown wire should go to "B", the red to "R", etc.
Connect the stepper motor wires to the adapter, which is connected to the board.



On your computer, head to the editor, and click the "Machine Controls" button on the top right. The click "Connect to Machine". 

On the pop-up, select your blot. It might be labeled as XIAO RP2040 or similar

Once it's connected, go back to machine controls and click pen down. Put the toolhead on the servo as shown.



Place the pen in the holder, and tighten the screw



Finally, head to the machine conrtols and hit run machine

# Tuning

You'll need to tune your blot after assembly, and every once-and-a-while when it's drawing something incorrectly.

We recommend using the [Blot logo](./test_pattern.js) as a test image. It's a good way to see if your blot is drawing correctly, with a good variety of straight, curved, & diagonal lines.

If well tuned, it should end up looking something like this:



**My blot only draws in diagonal lines!**

This probably means that only one of your motors is turning correctly take the belt off your blot and hold each motors axle to see which motor is behaving, erratically or weekly. ￼



**Blot only vibrates instead of moving**

This is a sign that your stepper motors are either wired incorrectly or don’t have a good connection.
- Unplug and replug your stepper motors.
- Make sure your stepper motors are plugged in the correct direction. The red wire should connect to the side labeled "red".
- Make sure the stepper motor horizontal breakouts are connected. Steppers **do not** directly connect to the main board.

**My blot draws weirdly**



This usually means your belt is not tight enough.
- Check if your belt pulley is attached tight. While your blot is powered on, try twisting the pulley. If it moves, it's not tight enough.
- To tighten it, use your smallest allen key to tighten both screws
- If your pulley is tight, try tightening the belt
- Move the belt clip forward. Attach the belt to the clip as tight as possible. Pull the belt clip as much as possible. Screw it in place.

**My belt keeps getting loose**

Ensure that the t-nut is 90 degrees from the alluminum extrusion



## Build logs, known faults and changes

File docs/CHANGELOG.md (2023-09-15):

# Changelog

This is a list of weekly developments for the drawing-thing updated every week.

## 2023-06-06 - @leomcelroy

I've gotten into running proper jobs on the machine and debugging whatever comes up.

Arpan posted a few programmatic drawings that he made. A few of us with machines started making them.

Here are some of my attempts:



And some of Hugo's:



I also tested some drawings from [PlotterFiles](https://plotterfiles.com/), like the one below.



The first issue I encountered was the line interpolation function hanging in the firmware when moving to points very close to zero. I naively fix this just by adding a maximum number of steps to the while loop.

```
int count = 0;
while (abs(motor1Step) < abs(motor1Target) || abs(motor2Step) < abs(motor2Target)) {
  if (count > 1000000) break;
  count++;
  ...
}
```

I was finding it difficult to debug with the cobs encoded messages coming up from the device so started using cobs encoding to send messages but using new line (`0x0A`) delimiters to differentiate messages being sent back.

The print function is useful for debugging arrays.

```
void printArray(String label, uint8_t* arr, int arrSize) {
  Serial.print(label);
  Serial.print("-BEGIN: ");
  for (int i = 0; i < arrSize; i++) {
    Serial.print(arr[i]);
    Serial.print(", ");
  }
  Serial.print(label);
  Serial.println("-END");
}
```

Unfortunately the firmware was still hanging frequently. My friend Jake Read suggested that the bytearray I was sending in the acknowledgement may be getting corrupted and I should try allocating it statically. To make this a bit easier I decided to remove sending variable length responses in the ack payload. The adjusted code with some remnants of the old code can be seen below.

```
const int arrayLength = 7; // + length;
static uint8_t byteArray[arrayLength];

void sendAck(uint8_t msgCount, uint8_t* reply, uint8_t length) {
  // Serial.println("SEND ACK");

  // int arrayLength = 7; // + length;
  // static uint8_t byteArray[arrayLength];

  byteArray[0] = 0x03;
  byteArray[1] = 0x61;
  byteArray[2] = 0x63;
  byteArray[3] = 0x6B;
  byteArray[4] = 0x00;
  byteArray[5] = msgCount;
  byteArray[6] = 0x0A;

  // byteArray[4] = length;
  // for (int i = 0; i < length; i++) {
  //   byteArray[i+5] = reply[i];
  // }
  // byteArray[5+length] = msgCount;
  // byteArray[6+length] = 0x0A;

  // Serial.println(msgCount);
  // printArray("ACK", byteArray, 5+length);

  Serial.write(byteArray, arrayLength);

  // uint8_t byteArrayEncoded[arrayLength + 2]; // +2 for possible COBS overhead
  // cobs_encode(byteArrayEncoded, byteArray, arrayLength);
  // Serial.write(byteArrayEncoded, arrayLength + 2);

  // printArray("ENCODED-ACK", byteArray, 5+length);

}
```

So far this has worked pretty well for me, but Shawn is still reporting some issues so we need to run more tests.

Moving on to some other parts of the project. I wrote up a [doc describing an engagement model](https://github.com/hackclub/haxidraw/blob/main/ENGAGEMENT.md) for gettine the machine.

Part of that model involves submitting pieces to a virtual gallery space. I decided an interesting space could be a infinite maze which gets randomly populated with submitted art work. I made a quick implementation of the maze which ended up being a classic raycasting project. Right now it's very Wolfenstein.

243733376-f5eefed6-7b86-4d67-b5d4-550e8e094344

## 2023-05-26 - @leomcelroy

Over the last two weeks I built a drawing interface/web editor for controlling the machine, added acknowledgments to the communication system, added COBS encoding and decoding.

Here is the draft interface:



I created two ways to make drawings. One is using the Turtle class which lets you create drawings programmatically, and two is by dropping an SVG into the editor which will automatically be converted into a Turtle. You can then use affine transformations (scale, rotate, translate) to position it properly.

In the bottom right corner the editor has a little console. This was somewhat interesting to implement. I wanted it to have access to the functions in the top-level scope of the most recently run script. So you can define functions in the editor and then run them on command in the command line. I did this by rewriting the script a bit before running it.

Here is the relevant code:

```js
const ast = acorn.parse(code, { ecmaVersion: 'latest' })

const topScopeInserts = []

ast.body.forEach(statement => {
  const { type } = statement

  if (type === 'VariableDeclaration') {
    statement.declarations.forEach(x => {
      topScopeInserts.push(x.id.name)
    })
  }

  if (type === 'FunctionDeclaration') {
    topScopeInserts.push(statement.id.name)
  }
})

topScopeInserts.forEach(name => {
  code += `\n;topScope["${name}"] = ${name};`
})
```

One design consideration when making the editor is that when a user calls the `runMachine()` function it should run the drawing which is currently visible.

Moving on to the firmware. It took a bit of patience to implement COBS properly. Though implementing it in JavaScript recently I willfully ignored doing so for the embedded instead opting to use newline delimiters for the communication stream. The ASCII for newline is `0x0A` otherwise known as 10. 10 periodically does show up in bytesteam encodings, which was giving me some trouble. This is what COBS is for, to give you a known unique character which will occur only at the end of your messages. The challenge in implementing it is my Arduino print statements (my primary debugging technique) no longer worked because the other end of my serial communication connection in the browser was then expecting 0 delimited messages.

The solution is pretty straightforward though. Just implement the encoding and decoding incrementally. So first verify I can encode and decode messages just in JS. Then send encoded messages to the firmware but expect to receive back newline delimited messages so I can read the print statements. Then when I know everything else works encode the messages coming back up and decode them in JS.

I ended up using this pattern frequently for inspecting the packets:

```cpp
Serial.print("RECEIVED: ");
for (int i = 0; i < bufferIndex; i++) {
  Serial.print(msgBuffer[i]);
  Serial.print(", ");
}
Serial.println("DONE");
```

I acquired some Gelly Roll Sakura pens which I used to make some of our most intentional drawings yet.



## 2023-05-15 - @leomcelroy

I made the JS controls function asyncronously by adding a number ID to each message and sending back acknowledgements. This allows us to write code like such:

```js
const port = await createWebSerialPort(rawPort)
const bytes = floatsToBytes([x, y])
await port.send('go', bytes)
```

in which the machine actually executes and finishes the command before the await resolves.

In the firmware I have a list of `EventCallback` structs.

```c++
typedef void (*CallbackFunction)(uint8_t*, int);

struct EventCallback {
  String event;
  CallbackFunction callback;
};

const int MAX_EVENTS = 255; // Maximum number of events to store, adjust as needed
EventCallback eventCallbacks[MAX_EVENTS];
int eventCount = 0;

void on(String event, CallbackFunction callback) {
  if (eventCount < MAX_EVENTS) {
    eventCallbacks[eventCount].event = event;
    eventCallbacks[eventCount].callback = callback;
    eventCount++;
  } else {
    Serial.println("Max number of events reached. Cannot register new event.");
  }
}

bool triggerEvent(String event, uint8_t* payload, int payloadLength) {
  for (int i = 0; i < eventCount; i++) {
    if (eventCallbacks[i].event == event) {
      // want to pass payload and payloadLength, need to get response payload
      eventCallbacks[i].callback(payload, payloadLength);
      return true;
    }
  }

  Serial.println("No event registered.");
  return false;
}
```

You may notice this is still somewhat incomplete as I'm not sending back response payloads. This could be added fairly easily though I don't actually have a need for it now. I was also planning to use interrupts but haven't completed that yet. I got a bit sidetracked testing writing firmware with other languages. Specifically Nim and TinyGo.

Both were fairly easy to set up. I used [piconim](https://github.com/EmbeddedNim/picostdlib) for Nim and TinyGo just worked out of the box (https://tinygo.org/docs/reference/microcontrollers/xiao-rp2040/). So far TinyGo has the cleanest development experience. After downloading the compiler you just need to use these two commands to build UF2s

```
tinygo build -target=xiao-rp2040 -gc=none -o hello.uf2 ./test.go
```

or flash UF2s

```
tinygo flash -target=xiao-rp2040 ./test.go
```

## 2023-05-08 - @leomcelroy

It looks like we'll be using the single control board designed for the drawing machine in the version we ship. Consequently I'm writing the firmware for this specific machine. Some design considerations:

- We should still be able to interface with the machine in high-level languages as a virtual object.
- The motor control should be good

These two goals and our approaches to addressing them are heavily influenced by the work we did the Modular Things project. For the first goal we need to define a communication interface. Almost like a REST API for the machine (if you're coming from the web dev world).

Motor control is a tricky topic. Historically most digital fabrication machines have been built around [GRBL](https://github.com/grbl/grbl) recently [Klipper3D](https://www.klipper3d.org/) has risen in popularity.

The basic problem is about figuring out how to turn multiple motors who's collective motion results in the movement of the machine in a controlled manner. In the case of our machine we have two motors which are coupled together through a belt.

In short I managed to write a fairly low quality motion controller (but a functional one) which has constant speed. Preferably we would set maximum accelerations and the planner would figure out the appropriate speeds based on the path it needs to take. But we'll build up to that in the coming weeks. We are sending out machines to testers and developers now so we need to have a nice interface for people to develop devices.

Something like this:

```js
import { createHaxidraw } from 'createHaxidraw.js'

await haxidraw.servo(-90)
await haxidraw.moveTo(x, y)
```

This is a virtual machine which communicates with the actual machine through the serial port.

On the other side of this communication is the firmware. I took five passes on this and ultimately made one that does the right thing by using Bresenham's Line Algorithm to coordinate the stepper motor motion. The relevant code is below:

```c++
void goTo(float x, float y) {
    // Set your target distances for each motor (in steps)
  float motor1Target = (x + y) - pos[0];
  float motor2Target = (y - x) - pos[1];

  // Set motor direction based on target values
  digitalWrite(motor1DirPin, motor1Target >= 0 ? HIGH : LOW);
  digitalWrite(motor2DirPin, motor2Target >= 0 ? HIGH : LOW);

  // Calculate the relative speeds and maximum duration for both motors
  float maxSteps = max(abs(motor1Target), abs(motor2Target));
  float motor1Speed = abs(motor1Target) / maxSteps;
  float motor2Speed = abs(motor2Target) / maxSteps;

  unsigned long stepDuration = 500; // The time it takes to perform one step in microseconds
  unsigned long motor1StepInterval = stepDuration / motor1Speed;
  unsigned long motor2StepInterval = stepDuration / motor2Speed;

  // Initialize variables for step timing
  unsigned long motor1PrevStepTime = 0;
  unsigned long motor2PrevStepTime = 0;
  float motor1Step = 0;
  float motor2Step = 0;

  // Loop until both motors reach their target steps
  while (abs(motor1Step) < abs(motor1Target) || abs(motor2Step) < abs(motor2Target)) {
    unsigned long currentTime = micros();

    // Motor 1
    if (abs(motor1Step) < abs(motor1Target) && currentTime - motor1PrevStepTime >= motor1StepInterval) {
      digitalWrite(motor1StepPin, HIGH);
      delayMicroseconds(1);
      digitalWrite(motor1StepPin, LOW);
      delayMicroseconds(1);

      motor1Step += (motor1Target >= 0 ? 1.0 : -1.0)/SPU;
      motor1PrevStepTime = currentTime;
    }

    // Motor 2
    if (abs(motor2Step) < abs(motor2Target) && currentTime - motor2PrevStepTime >= motor2StepInterval) {
      digitalWrite(motor2StepPin, HIGH);
      delayMicroseconds(1);
      digitalWrite(motor2StepPin, LOW);
      delayMicroseconds(1);

      motor2Step += (motor2Target >= 0 ? 1.0 : -1.0)/SPU;
      motor2PrevStepTime = currentTime;
    }
  }

  pos[0] += motor1Step;
  pos[1] += motor2Step;
}
```

Ella and I ported some of the interfaces from Modular Things to be stand alone web-pages.

Using the Turtle drawing tool I managed to get some images which came out more or less as intended.

PXL_20230506_055516518 (1)

Next I'm going to use interrupts to make the movement code non-blocking in the firmware and have the JS messages properly await confirmations (or "acks") from the machine.

## 2023-05-01 - @exu3

Last week, we recevied the control boards from JLCPCB, and I assembled a few. I documented the components and assembly process in [`motor-control-board/`](./motor-control-board/README.md). Here's a photo of what the board looks like:

assembled control board

The next step would be writing firmware for this board so that it can be used in the modular-things editor.

I also wrote an assembly guide for the drawing machine so people can start building them. It can be found in [`drawing-thing-v2/ASSEMBLY.md`](./drawing-thing-v2/ASSEMBLY.md). The Bill of Materials, adding line numbers which correspond to the various bags of hardware that people will receive the drawing machine parts in.

## April 2023 - @leomcelroy

Not directly about the development but during this month I went to two conferences where I shared the machine. You can read about them in my Slack posts here:

https://hackclub.slack.com/archives/C04GCH8A91D/p1681746685468929

and here:

https://hackclub.slack.com/archives/C04GCH8A91D/p1682972980825199

## 2023-04-03 - @leomcelroy

Big updates from last week!

I decided to make a single control board to make it easier to send people supplies to complete due diligence on what the cheapest version of the machine might be. A contributor to SVG PCB recently submitted some PRs adding excellent Gerber support so I took great satisfaction designing the boards in my own CAD tool and ordering them from JLCPCB. You can find the design [here](./motor-control-board/). You can also play with the [design in the SVG-PCB editor here](https://leomcelroy.com/svg-pcb/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).

Here is a picture of the board.

anon (29)

We've made heaps of pen holders but none were stiff enough. Not anymore! By 3D printing a rail and using a similar v-wheel carriage design to the rest of the machine we were able to make this slick little servo-driven z-axis which works very well. I'm extremely pleased with this design!



Thanks to finally having a good pen holder we were able to put together a well functioning complete machine. Conveniently this happened on the day Ella came to visit cambridge so we got to run it together.

We also wrote a [small Turtle drawing library](./editor-examples/turtle.js) which can drive the machine. You can first visualize what you will draw in the editor and then run the machine.



Here are some shots of the complete device below.










## 2023-03-28 - @leomcelroy

This week I released a toy re-implementation of the networking library we are using for modular things.
You can find this library here [modular-things/nosap](https://github.com/modular-things/nosap).
The point of this is better understand what [OSAP](http://osap.tools/) (current JavaScript implementation [here](https://github.com/jakeread/osapjs/tree/main)) does and what it needs to do.
Primarily it's a library for packing and routing messages across devices.

It differs somewhat from what Jake (the original OSAP author) describes in his [approach](http://osap.tools/approach/) for the sake of making things simpler and easier to comprehend.
Hopefully these difference will diminish in the near future.
In a series of long conversations with Jake I've come to better understand OSAP itself and I believe to persuade him to remove notions of hierarchy from the graph design.

I'd like to make a visualizer for networks in the toy implementation which can be used to investigate actual OSAP networks in the future. Which brings us to another thing we worked on last week.

We released a [TODO list](https://github.com/hackclub/drawing-thing/blob/main/TODO.md) to help people find ways to participate in the project. This will evolve into proper GitHub issues with good project management but we started just by dumping thoughts and tasks into this Markdown document.

## 2023-03-20 - @leomcelroy

This week we tested some resin parts, built two pen holders, and published the BOM (bill of materials) for the most up to date machine design.

We ordered the parts from [JLCPCB's 3D printing service](https://jlcpcb.com/3d-printing) which is amazingly cheap and quick. The concern using resin prints over FDM ones is that resin tends to be more brittle. The print quality is very nice and consistent though so the verdict is still up in the air.

A friend Rob Hart helped design a sliding mechanism for a pen holder with very few parts. It uses 3 little posts on compliant levers which act as little springs holding the moving portion of the design in place. The other pen design is an adapted version of the lever which B. Smith used all the way back in our v0 prototype. You can see both of these designs in the photos below.

Below is the full slider machine with resin parts:

slider

Here is the front of the slider:

front slider

Here is the inner portion:

inner slider

Here is the same machine with a lever pen holder:

lever

I also organized and published the materials and STL files for this current machine design. [The BOM can be found here](https://github.com/hackclub/drawing-thing/blob/main/BOM.md).

## 2023-03-10 - @leomcelroy

> https://hackclub.slack.com/archives/C04GCH8A91D/p1678497440093879

Time for this week's update! We've got yet another rework of some key parts of the design.

First, those who have been following know I've been battling for weeks with making the motor brackets stiffer so they don't bend under loads from the belts. They were starting to get a bit chunky when what I really wanted to do was make the side supports taller. You can see in the second picture I was able to thin out the material and make the stiffest bracket yet. I also made the lever the belt pulls on a bit shorter by moving the motors closer to each other. The two main wins in decreasing the distance were removing some extra material where the aluminum extrusion attaches to the rest of the bracket and moving the foot to the other side (so it's no longer between the motor and the plastic).

The biggest change yet is we're testing a 3D printed carriage design. It won't be as stiff as the sandwiched metal plates but it should be stiff enough and it's much easier to assemble. I was able to knock more than 10 parts off the bill of materials (BOM) with this.

I also spent some time with our collaborators at MIT looking at the networking system used among the boards in the machine. I started to implement it from scratch to test my own understanding and to see if there are parts we can simplify. One of the most interesting parts was learning about [consistent overhead byte stuffing](https://en.wikipedia.org/wiki/Consistent_Overhead_Byte_Stuffing).

Looking forward we still need to sort out our pen holder, design a custom connector for board-to-board communication, figure out power delivery (right now everything is powered by 5V), and put the whole system through its paces.

latest development of machinestiffer motor brackets

## 2023-03-03 - @exu3

> https://hackclub.slack.com/archives/C04GCH8A91D/p1677875892149909

This week, I got the latest version of the 2d-cut parts fabricated using metal for a better test to see how the machine flexes/bends/moves when tensioned. I sent the DXF files to a super cool local manufacturing company to get them fabricated. The pieces were cut from 1/4" thick aluminum on a waterjet, then sandblasted to remove burr.

machine with metal plats and feet

## 2023-02-24 - @leomcelroy

> https://hackclub.slack.com/archives/C04GCH8A91D/p1677285634597069

Time for this week's update. The hardware design is starting to anneal. The key thing I've been paying attention to is how belt tension bends/twists parts of the device. This is primarily an issue on the side motor brackets. You can see how it's been beefed up in the first image.

In addition to Ella's pen holder we experimented with a minimal part sliding design which you can see in the second image. Thanks to Rob Hart for assisting with this one.

Ultimately the flat pieces (carriage plates and feet) will be made out of metal. Consequently they'll be much stiffer than the current plates which bend (causing the wheels to wiggle) if you stick out floating axis arm and press on it. In order to get a more representative test I cut some plate from Delrin on a ShopBot (seen in image 3). The best test though would just be to have them fabricated from aluminum as the design intends. I'll try an order for that next week.



delrin on shop bot

## 2023-02-17 - @exu3

> https://hackclub.slack.com/archives/C04GCH8A91D/p1676690988312429

This week’s update in development of the drawing thing includes the fabrication yet another prototype and improvements correcting some issues. The images below are the CAD models of latest prototype. Notable revisions include:

- Using flanged bearings instead of normal bearings inside the 3D printed idlers. I found the normal 625 bearings a bit difficult to fit inside the idlers and cracked some plastic idlers in the process of getting them in.
- The carriage is now a sandwich, which helps with making it more stable. In previous designs, it was a flexing a bit. Adding the extra v-wheel was also helpful.

I also thought about a new design for the pen holder. Specifically using a compliant mechanism, to reduce the number of parts needed, and because I think they are cool. I haven’t fabricated this part yet, but it will be one of my objectives for the week ahead.

3d model of machine prototype 3d model of machine prototype

## 2023-02-10 - @leomcelroy

> https://hackclub.slack.com/archives/C0M8PUPU6/p1676083722576069

Here's another update on the drawing machine @Ella and I are making. You can follow along in #development-of-things-and-stuff.

This week we made another prototype design (1st photo), fabricated it, then yet another prototype design correcting more issues we found. The improvements involved 3D printing idlers with 625 bearings inside in order to reduce part count and hone in on the dimensions we need to align the belt. The belt sits in a cross formation which allows two motors to control the x and y motion through coupled kinematics. The idlers sit on the carriage which moves and redirect the belt along each side of the perpendicular axis. You can see this in the 2nd photo below.

The main issues with the design we fabricated this week were the whole machine tipping because the feet had too narrow a base, the belts being misaligned, and the carriage flexing. In the third photo you can see we made the machine more stable by adding wider feet, we repositioned the idlers to align the belts, and we also swapped the double beam for a single one (plus added an extra v-wheel) to help with the carriage flexing issue. In the final machine we'll probably make the carriage plate out of aluminum with a service like SendCutSend which will make it much stiffer than our 3D printed prototypes.

Ella also made a very nice pen holder (4th photo) which cleverly uses nails as rails.

I took a pass at creating an SVG importing interface within the modular things editor. You can import svgs which get separated based on color, then rearrange them and apply some basic affine transformations to them. This is the start to an interface for dropping in vector drawings which the machine will then make.

Very excited to start making art with this soon!

3d model of machine prototypemachine wheels
machine with improved feet designpen holder that uses nails as rails

## 2023-02-03 - @exu3

> ohyeah it's a drawing-thing

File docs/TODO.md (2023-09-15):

# So many things TODO

There are many tasks left in the development of our drawing machine which will become one of the best ways to get into digital fabrication. We are rethinking and remaking how hackable these types of machines can be with the [Modular Things project](https://github.com/modular-things/modular-things). Tasks range from [mechanical design](#mechanical), to [low-level firmware](#firmware), and [high-level interfaces](#editor).

Below is a list of various things we are working on, and ways you can engage with the tasks at hand or the associated concepts.

## Hardware

### Mechanical

~~**Design a pen holder.**
We still need to finalize the part that makes this machine a drawing machine, the pen holder!
We put out an open challange to help with this which you can find [here](https://gist.github.com/exu3/e5c1469467667c8790b3f5bda7172f39).~~

**Build your own machine.**
You can already build your own machine if you have access to a 3D printer.
The [bill of materials can be found here](https://github.com/hackclub/drawing-thing/tree/main/drawing-thing-v2).

### Electrical

> The Modular Things hardware repo is at https://github.com/modular-things/modular-things-circuits.

**Remake the circuits in SVG-PCB.**
The [circuits used in the system are designed here](https://github.com/modular-things/modular-things-circuits).
I would love to see people remake the circuit designs in [SVG-PCB](https://leomcelroy.com/svg-pcb-website/#/home).

**Create a board-to-board link layer.**
We don't have anyway to connect boards to each other. Right now they are all connected to the computer through USB.

**Create a [bus](<https://en.wikipedia.org/wiki/Bus_(computing)>).**
Currently our system uses point-to-point connections.
It would be more efficient to design a bus (one-to-many connection) for modular things.
Some thoughts on [bus design for modular things are available here](https://github.com/modular-things/modular-bus).

## Software

> The software can be found at https://github.com/modular-things/modular-things.

### Firmware

**Sequential motor control.**
https://github.com/modular-things/modular-things/blob/main/src/lib/virtualThings/synchronizer.js
We need smoother motion for our machine.
Right now we stop at each corner; it would be better to interpolate between them.

**Klipper Style Motion Planning**

**Clean up OSAP the networking library.**
https://github.com/modular-things/modular-things/tree/main/src/lib/osapjs
Jake and Leo are working on making OSAP more comprehensible.
Leo made a [toy implementaion recreating some of OSAP's functionality](https://github.com/modular-things/nosap).
Making a visualizer for OSAP networks would be a great project.

### Editor

**Add console to the editor.**
Right now when you run a program in the editor it runs everything.
A console would allow you to run select functions and also log outputs.
[@pranavnt](https://github.com/pranavnt) is working on this.

**Create interface to drawing machine in the modular things editor.**
Here is some [skeleton for an interface](https://github.com/modular-things/modular-things/blob/main/examples/machine-interface.js) which isn't hooked up to any machine.

## Engagement (Interaction Mode/Handles)

**Make a parametric art generator.**
You can also get started working on generative design and pen plotting.
[Drawingbots](https://drawingbots.net/) is a good resource.
Specifically the [tool section](https://drawingbots.net/knowledge/tools) has a bunch of programs for making plottable patterns.

**Make some parametric art.**
Make some generative art which could be drawn by a plotter. For some examples of this check out [the blogs linked at the bottom](#general-inspiration).

Last year I made a [basic Turtle drawing editor](https://microworlds.hackclub.dev/?file=turtle) as part of the microworld project at Hack Club. As an aside the idea with this project was to create a series of workshops in the form of [microworlds](<https://en.wikipedia.org/wiki/Mindstorms_(book)>). These workshops integrated a small library for making a specific type of thing, a live-editor and visualizer for that library, documentation, and some easy sharing tools.

The Sprig editor is another microworld and we'll almost certainly make one for this project too.

**Gallery for parametric generators and art.**
_Functional_ designs and generators with coherent and consistent interfaces.
Something like [Printables](https://printables.com) but with the source for the designs available.

### Weekly Updates

Each week or so we post an update to our [`CHANGELOG.md`](./CHANGELOG.md).

## General Inspiration

Here are some blogs about plotting which are worth checking out:

- https://revdancatt.com/
- https://penplotterartwork.com/
- https://greweb.me/
- https://targz.fr/
- https://larswander.com/
- https://www.v3ga.net/
- https://bylr.info/
- http://andymakes.com/#Plotter
- https://www.eyesofpanda.com/
- https://mattdesl.svbtle.com/pen-plotter-1
- https://muffinman.io/art/

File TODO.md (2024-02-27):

- syntax highlighting of markdown
- cmd s save, auto save
- check session length
- sort files by age
- share link
- error handling
- delete and rename files
- favicon
- port header
- automatically generate bundled css import
- make sure bundle path is correct
- css modules -> tailwind?
- remove 
  - unused icons in src/ui
  - [x] unused assets in /public
- [ ] file renaming
- build tailwind
- errors without line numbers shouldn't highlight

- questions to answer
  - new Turtle vs createTurtle
  - chain vs functions
  - lines vs polylines
  - how to add everything to global scope
  - whether to import toolkit
  - how to get path from turtle
  - long imports are a drag

- link to reference
- cheatsheet autogen from the reference
- toolkit could be collapsed version
- anchors in two different documents
- anchors for function names themselves and sections in reference
- include image of examples in reference
- turtle angle is right not up
- turtle angle is called angle not heading
- where is 0,0
- where is the bounds of where to draw
- what is the scale
- simulation of how blot will draw it out
- turtle path called path (not lines, polylines)
- ending angle
- in line drawing animation show the coordinates being drawn

- highlight points to manipulate

- [x] fix guide import
- [x] import errors don't have line numbers
- [x] add accounts

- comments and whitespace above import mess up error lines
  - because I was taking white space before import
- import mapping doesn't support "as" renaming

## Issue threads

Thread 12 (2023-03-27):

[software/gallery] Gallery for parametric generators and art

exu3, 2023-03-27:
Gallery of function designs and generators with coherent and consistent interfaces.

###### ~~_plottables_~~

This issue tracks the the development of a gallery for community-built parametric art generators and art, similar to [Printables](https://printables.com/) but with the source code available. The details are yet to be fleshed out but ideas are welcome.

leomcelroy, 2023-06-29:
We've got a maze right now but a flat gallery will be good too.

Closed 2023-06-29.

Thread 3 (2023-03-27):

[hardware/mechanical] Fabricate a machine

exu3, 2023-03-27:
You can build your own "drawing-thing" machine if you have access to a 3D printer. The bill of materials can be found in [`BOM.md`](https://github.com/hackclub/drawing-thing/blob/main/BOM.md).

You can also find the STLs for 3D printing on Printables: https://www.printables.com/model/425878-drawing-thing-v10-3d-printed-carriage

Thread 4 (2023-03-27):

[hardware/electrical] Make the Modular Things circuits in SVG-PCB

exu3, 2023-03-27:
The Modular Things circuits can be found [here](https://github.com/modular-things/modular-things-circuits). This issue tracks the translation of those circuits to [SVG-PCB](https://leomcelroy.com/svg-pcb-website/#/home), an in-browser editor that lets you design a PCB from a JavaScript code description.

leomcelroy, 2023-05-26:
We're going to ship one board with the machine so I'll close this as not planned.

Closed 2023-05-26.

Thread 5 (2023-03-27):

[hardware/electrical] Create a bus

exu3, 2023-03-27:
**Create a [bus](https://en.wikipedia.org/wiki/Bus_(computing)).** Currently our system uses point-to-point connections. It would be more efficient to design a bus (one-to-many connection) for Modular Things. Some thoughts on [bus design for Modular Things are available here](https://github.com/modular-things/modular-bus).

###### it seems the repo is private.....

leomcelroy, 2023-05-26:
Shipping one control board with our machine means we won't need this. In the long term is still a good thing to do but not in our critical path.

Closed 2023-05-26.

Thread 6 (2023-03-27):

[software/firmware] sequential motor control

exu3, 2023-03-27:
We need smoother motion for our machine. Right now we stop at each corner; it would be better to interpolate between them.

https://github.com/modular-things/modular-things/blob/main/src/lib/virtualThings/synchronizer.js

leomcelroy, 2023-05-26:
The current code for the firmware is here: https://github.com/hackclub/haxidraw/blob/main/motor-control-board/firmware/firmware.ino

Closed 2023-10-20.

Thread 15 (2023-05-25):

Documentation and Build notes

Sheepy3, 2023-05-25:
issues I had (probably not my fault?)
- numbers on bags dont mean anything
- screws arent labled with their size, so I had to use a caliper to confirm. maybe include a printout with 1:1 labeled screws so one could just hold the screw up to the sheet and see if it's accurate?
- dent/scratch in aluminum extrusion causes resistance when core moves along it.
- nuts on top and bottom at the same time cause problem where the nuts fall out. the instructions should call for nuts on the bottom first, screw in the flanged bearings, then the top ones.
- no instructions on the flange nuts and how to properly install them. (spent a lot of time trying, in hindsight, very silly ways to put them in. I could have saved like 20 minutes if there was a better explanation.)

nitpicks
- bags have varying screw colors and lengths, shouldn't matter if there's a disclaimer so people don't get confused
cant click on images in the instructions, made it a bit of a bother to open images in a new tab (2 entire seconds of my life, gone...)
- why no spacers used on attachment of feet to motor
- which way is the servo supposed to go? (I eventually figured this out)
- no mounting solution for the driverboard, and new screw holes for potential future mounting solutions

need to update documentation based on feedback

Sheepy3, 2023-07-18:
updates to v3 solve issues on too many screws, and I will take on instruction issues. hope to design a haxidraw drawing that acts a little size guide for the screws.

Sheepy3, 2023-07-27:
closing this issue as i feel all it's aspects are covered individually by newer issues

Closed 2023-07-27.

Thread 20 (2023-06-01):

PCB update

leomcelroy, 2023-06-01:
- Larger heat dissipation planes
- Silkscreen layers

karamassie, 2023-06-12:
@Hugoyhu pls remember to get leo to review your designs (and post in the main haxidraw channel )

Closed 2023-06-29.

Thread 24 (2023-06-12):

design improved pen holder compliancy

karamassie, 2023-06-12:
some plotters have a way for the user to add pennies for weight. let's try this.

karamassie, 2023-07-03:
@leomcelroy is this being reassigned?

Sheepy3, 2023-08-20:
experimented with compliant design, but got dimensions wrong. designed an eccentric-spacer design to be shipped if the compliant design is not finished in time for release

Sheepy3, 2023-09-13:
designed compliant design, has not been tested extensively. will potentially run tests on it when i have a new board and a spare blot. for now, petg testing is prioritized.

Closed 2023-09-25.

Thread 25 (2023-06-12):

add mounting for control board

karamassie, 2023-06-12:

Sheepy3, 2023-07-27:
first test-ready version done, waiting new pcb's to iterate

Sheepy3, 2023-09-09:
waiting on new-new pcb's to arrive to create new version with new mountain for blot v4

Sheepy3, 2023-09-22:
board mounting mechanism designed, designing rail mounting design

Sheepy3, 2023-09-25:
designed initial iteration of pcb mount, refining. Will push a version on monday

Sheepy3, 2023-09-25:
uploading a version of the pcb mount

Closed 2023-09-25.

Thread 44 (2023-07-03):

clean up CAD model

karamassie, 2023-07-03:
- improved PCB mount and shoes (please work with @Sheepy3  )

Sheepy3, 2023-07-18:
testing assembly of v3 parts today. will see if theres anything that can be optimized. in terms of printability, @Merlin04 has already done an excellent job with their additions. design cohesivity (consistency of curves vs sharp edges etc) may need another pass, would love help with that

Sheepy3, 2023-09-09:
did pass on design cohesivity for pen holder, printed rail + motor holders probably need some curves on the edges

Closed 2023-10-09.

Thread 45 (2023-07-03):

design new feet

karamassie, 2023-07-03:
pls work w/ @Merlin04

Sheepy3, 2023-08-20:
feet have been integrated into the motor mounts, and single-rubber-pad holders have been added. will test on monday

Closed 2023-08-28.

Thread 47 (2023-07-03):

Update assembly guide

karamassie, 2023-07-03:

Sheepy3, 2023-08-20:
will begin taking pictures and writing down notes on assembly on monday, following completion of haxidraw v4

Sheepy3, 2023-09-09:
closing this, see issue #69

Closed 2023-09-09.

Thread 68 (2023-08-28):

create shipping procedure

leomcelroy, 2023-08-28:
- how to package machines
- need to buy boxes

Sheepy3, 2023-09-21:
ordered sample filament, sample wheels

Sheepy3, 2023-09-26:
sample package arrived, but I am not positive on this box being the best for the machine. I'm going to look into more samples before I go home for the day, but will come to a decision soon as we near the end of october.

Sheepy3, 2023-11-20:
ordered 100x boxes whiich are a lot nicer than the one tested in september

Closed 2024-02-16.

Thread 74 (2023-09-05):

Make settings menu line up

leomcelroy, 2023-09-05:
Recent changes have made the menu go from this

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

to this

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

The improvement is that it is triggered on hover and lines up a bit differently with the toolbar.

The digressions which should be corrected are:

- the settings icon is not centered on the top toolbar anymore
- the menu options should be on one line each as before

Closed 2023-09-07.

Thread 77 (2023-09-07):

add missing parts to machine sim

leomcelroy, 2023-09-07:
- screws
- gears
- belt
- pen
- servo

leomcelroy, 2023-09-12:
@Sheepy3 can you provide us with these models so we can add them to the website

Sheepy3, 2023-09-21:
repairing assembly in onshape. so far:

-updated carriage with eccentric spacers
-added missing screws to upper rail
-updated pen holder with eccentric spacer

Sheepy3, 2023-10-16:
no longer using machine sim?

Closed 2023-10-16.

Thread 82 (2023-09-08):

print parts in petg

leomcelroy, 2023-09-08:

Sheepy3, 2023-09-09:
print failed, waiting on enclosure and drybox to arrive before testing again. also need to try using prusaslicer

Sheepy3, 2023-09-18:
printed blot in petg on thursday of last week. will assemble and begin running machine for 100hrs this week

Closed 2023-09-18.

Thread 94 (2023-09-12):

run machine 100 hours

leomcelroy, 2023-09-12:
Make one in petg. Run it for a long time making lots of art. Report on what happens.

Sheepy3, 2023-09-21:
machine made in prusament petg, awaiting board from Hugo in order to test. when spool from printerior arrives, will produce a new blot in their filament and test that as much as possible. will likely need a dedicated computer connected for this purpose

Sheepy3, 2023-09-26:
started running tests on machine today!

Sheepy3, 2023-10-06:
machine has run at least 150 hours, with minimal wear. will continue to test past this

Closed 2023-10-06.

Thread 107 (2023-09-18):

assemble new board recieved from hugo

Sheepy3, 2023-09-18:
assemble and test new board received on thursday.

Sheepy3, 2023-09-19:
new board isnt actually the final board, waiting on new-new board which is currently in the mail.

Sheepy3, 2023-09-22:
recieved new board, assembled

Closed 2023-09-22.

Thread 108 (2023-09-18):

Rewrite README and upload KiCAD files /whatnot

Hugoyhu, 2023-09-18:
The circuit part for blot repo is outdated. will update with:
- newest carrier board
- fixed 9V1A cypd3177 board
- iamges!

KiCAD v7 sch, brd, schematic capture, BOM, PCB layout

Sheepy3, 2023-09-21:
could we get .svg's of the boards too?

Hugoyhu, 2023-09-26:
Yes, but not sure if those will look nice. I'll be happy to draw mechanical size charts
@Sheepy3 could you please DM me on this for what SVGs for etc. CLosing this issue for now

Closed 2023-09-26.

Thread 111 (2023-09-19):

Make an assembly video

leomcelroy, 2023-09-19:

Sheepy3, 2023-09-26:
will speak with dieter about doing a really nice assembly video in the near future

kcoderhtml, 2023-12-26:
Currently working on a video right now!

Closed 2024-07-11.

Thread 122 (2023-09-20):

Take glamour shots of machine

leomcelroy, 2023-09-20:
- make some gifs of it running

karamassie, 2023-09-21:
@Hugoyhu is also a fab photographer....

Sheepy3, 2023-09-25:
mailed him parts for a new machine last week, he could take some good pictures once it arrives. Though the quality of the prints of his machine may not perfectly represent the final product, I was still tweaking the printer's settings.

Hugoyhu, 2023-09-26:
I will do a photoshoot of blotty bot + related PCBs with my setup when I get my fab sunset orange PLA parts installed. Will keep you updated via slack and assigning myself to issue

leomcelroy, 2023-09-27:
Couple of specific shots we want

- a video of the machine running
  - drawing leaf, squiral, something nice
  - use a thick pen
  - do a couple takes at different angles
  - need to be able to remove background
- a shot of all the parts
- a shot of each part individually

Sheepy3, 2023-10-05:
finished shots of each part individually, finished shots of PCB

Sheepy3, 2023-11-01:
took shots of machine, were not high quality enough, will take shots again at next available time

Sheepy3, 2023-11-04:
scheduled time next week to take more photos.

Closed 2024-01-05.

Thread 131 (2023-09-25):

inconsistent camelcase

Sheepy3, 2023-09-25:
multi word functions like setAngle use camelcasing, but goto does not. should be goTo?

VivekChatterjee, 2023-09-25:
Yes, it should be good to have uniform camel casing everywhere.

leomcelroy, 2023-09-25:
It's funny because it's actually switched back and forth. Alright let's go with `goTo`.

We'll have to update the gallery and workshops

JCardona0110, 2023-09-25:
hello! i can take care of this issue

V205Arduino, 2023-09-25:
Hmm. Could it be made to be backwards compatible?
I have some code that uses goto,.....

recursiveforte, 2023-09-26:
now that I think of it… what if blot functions weren’t case-sensitive?

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

V205Arduino, 2023-09-26:
Should be following camel case.
What does sprig use?

leomcelroy, 2023-09-26:
Just update your code @V205Arduino

Closed 2023-09-26.

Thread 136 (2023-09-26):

add "reset zero" button

Sheepy3, 2023-09-26:
add a button to the interface which resets the 0,0 point to the current toolhead position, without needing to unplug the xiao.

Closed 2023-11-17.

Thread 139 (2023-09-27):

create homing procedure

leomcelroy, 2023-09-27:
- move blot to center
- draw a little image
- move to corner that it points to

leomcelroy, 2024-07-11:
added to new assembly/operation guide

Closed 2024-07-11.

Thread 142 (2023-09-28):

Add run fast, run, run step by step buttons in editor?

V205Arduino, 2023-09-28:
Add run fast, run, run step by step buttons in editor?
A bit like:
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

BrightTheBackpack, 2023-11-14:
I'm working on step by step, but what would run fast look like? Do you want the current run to run slower? Or do you just want me to add step by step

V205Arduino, 2023-11-14:
Hmm.
Run fast like instant run? So the drawing generates immediately?
I think we could do it like this:
1. Run step by step and run normal(instant or ?) or
2. Run step by step and run fast(instant)?
Probably just 1…….

BrightTheBackpack, 2023-11-14:
yeah probably #1.

BrightTheBackpack, 2023-11-14:
cause run normal is already instant so..

V205Arduino, 2023-11-14:
Ok, sounds great!

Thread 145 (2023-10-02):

double clicking run machine causes drawing to bug out

Sheepy3, 2023-10-02:

leomcelroy, 2023-11-21:
Run button changes to stop when running now.

Closed 2023-11-21.

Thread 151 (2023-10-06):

add support for older boards in firmware/editor

Sheepy3, 2023-10-06:
Older PCBs had different pinouts, which the newer firmware no longer supports. we either need firmware versioning or support for different pinouts in the editor

leomcelroy, 2023-10-12:
We only need to support the new boards.

Closed 2023-10-12.

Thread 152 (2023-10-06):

test carriage warping

Sheepy3, 2023-10-06:
reported issues of carriage warping. testing warping on a 40% infill 4-perimeter PETG carriage, by placing it under stress for an extended period of time.

Sheepy3, 2023-10-16:
will be receiving aluminum plate soon, will likely result in minimization of warping. as for current test running, not seeing any issues so far, but it has only been 2 weeks. we will most likely release the first run of blot's with the aluminum plate, and if we find that the newer designed parts do not suffer from warping, we can just stop giving people them.

leomcelroy, 2023-11-14:
This plan sounds good shawn. Going to close this for now. I'm happy with the plate I've used so far. Let's keep a design for the not plate version of the carriage so people can print machines if they want.

Closed 2023-11-14.

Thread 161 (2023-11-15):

Difference between editor preview and blot drawing when using Math.random()

maxwofford, 2023-11-15:
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

- It wasn't clear to me that I had to use `rand()` to prevent this because I hadn't scrolled to that part of the docs.
- I didn't realize I was using `Math.random()` because I copied code from an example implementation of a K-mean algorithm online

I'd propose fixing by prototyping `Math.random()` to give a warning on first usage. That'd help...
- warn people who don't know they need to use `rand()`,
- people who accidentally used `Math.random()` even though they know to use `rand()`

BrightTheBackpack, 2023-12-18:
if someone implements a warning system for different functions, can you also add a warning for print()? I once had a 100 long for loop and had to close the print page prompt 100 times.

maxwofford, 2023-12-19:
@BrightTheBackpack Want to create a new ticket for that? I think that's a separate discussion because `Math.random()` is something that we're treating different on our site. Things like `print()` `alert()` and `prompt()` can be prototyped, but that's more browser specific, not site specific.

maxwofford, 2024-07-15:
Just tested this and it's no longer erroring on submissions like this: https://blot.hackclub.com/editor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

Closed 2024-07-17.

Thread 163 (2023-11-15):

Unclear if machine is running

maxwofford, 2023-11-15:
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

The editor UI has a button to "Run machine", but doesn't have a way to tell if I've clicked it. After clicking and the machine not responding I can't tell if...

- I didn't click the button
- My script hit an error that didn't throw
- My script runs long and is still processing
- My script has an infinite loop
- There's a problem with the physical connection to the machine, or from the control board to the motors

leomcelroy, 2023-11-21:
It changes state now. Could show a progress bar to be improved more.

Closed 2023-11-21.

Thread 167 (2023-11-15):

Unexpected behavior when trying to share a piece

maxwofford, 2023-11-15:
I tried to send someone a link to a piece of art found in the gallery, but the link didn't work. Steps to replicate:

- Go to the gallery:
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
- Click on a piece
- Copy the URL of the piece in the editor

Expected behavior:
- The link I'm taken to can be shared with others
- The art I've been working on isn't overwritten
Actual behavior:
- I get the generic editor link that shows different content on someone else's computer
- My previous work has been overwritten

jianmin-chen, 2023-11-27:
Just flagging - this should work after PR #177 is merged.

leomcelroy, 2024-03-25:
#341 adds a share link button.

Closed 2024-03-25.

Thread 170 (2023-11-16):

Opening someone else's art deletes my work

maxwofford, 2023-11-16:
Replication steps:

- I clicked a piece in the gallery while my own was open in another tab.
- I closed my own tab
- I clicked "run" on the gallery art
- When I tried to reopen my own game, it was overwritten by the gallery art

Sheepy3, 2023-11-18:
is this just a result of not having a login system?

jianmin-chen, 2023-11-18:
I think so - currently we just automatically save whatever's in the editor to `localStorage`. IIRC the account system fixes that, let me check.

maxwofford, 2023-11-19:
Some of this could be fixed by an account system (ie. I can save), but I also want to flag https://github.com/hackclub/blot/issues/167. It seems like this is caused by trying to use the same URL for multiple states (ie. blot.hackclub.com/editor used for my file, and someone else's file).

Another example of the problem this ticket refers to is running 2 editors in 2 tabs next to eachother. I like to splitscreen and tweak a demo while building my own thing based on it.

ozan, 2024-01-18:
Perspective of a new user here: this is the most annoying part of an otherwise really lovely experience :) I keep wanting to work on my thing, but have somebody else's thing open too for inspiration etc, but this is not possible.

It seems like the current model of state is: single edited file per browser, persisted locally via `localStorage`. Have you considered using `sessionStorage` instead? That should give you the benefit of not losing changes while a tab is open, but also new state per tab.

(I actually made this fix locally... happy to PR but didn't want to step on anyone's toes)

leomcelroy, 2024-03-25:
It would be great if you PR'd that @ozan

leomcelroy, 2024-03-25:
I switched local storage to session storage as discussed above.

Closed 2024-03-25.

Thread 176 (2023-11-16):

Blot engine tab always has to be open for blot to run

nilaRam, 2023-11-16:
2 parts to this:

1- when switching desktops blot would pause (possibly a good safety feature)
2- when left open too long the screen sleeps & blot pauses (this doesn’t seem like a feature)

Sheepy3, 2023-11-18:
seems to be same as issue #173

Closed 2023-11-18.

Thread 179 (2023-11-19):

doing print() causes page print to occur when running

BrightTheBackpack, 2023-11-19:
Some people(like me) who are ultra familiar with python syntax may accedently do print() instead of console.log(). This results in the page print prompt to show up on chrome(haven't tested on any other browsers) when running.
```[tasklist]
### Tasks
```

kalpan-shah, 2023-11-19:
Hi @BrightTheBackpack  ,I'll say you will face that in any browser,( except your regular node native without browser) cause the JS print() invokes the printer utility in windows. so console.log() is the only way my friend you'll be able to make a simple print() just like python.

I know it's hard to switch the familiarity.

BrightTheBackpack, 2023-11-20:
I feel like there should be a warning before you click run if you have a print() statement.

Closed 2023-11-20.

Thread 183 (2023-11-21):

Tuning guide

maxwofford, 2023-11-21:
_or, "Now I've got my blot, how do I make it draw good?"_

I'm opening this based on [this thread](https://github.com/hackclub/blot/issues/166#issuecomment-1821674631). We probably want a documented guide on how to tune / fix the machine for users.

leomcelroy, 2024-03-25:
This is a work in progress will close this issue for now for housekeeping.

The current guide is available here: https://github.com/hackclub/blot/blob/main/docs/TUNING.md

Closed 2024-03-25.

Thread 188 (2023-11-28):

uf2 for firmware

Sheepy3, 2023-11-28:

leomcelroy, 2023-12-04:
Available here: https://github.com/hackclub/blot/blob/main/hardware/motor-control-board/firmware/build/rp2040.rp2040.seeed_xiao_rp2040/firmware.ino.uf2

Closed 2023-12-04.

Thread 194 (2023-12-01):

Dark mode or customizable pallette

maxwofford, 2023-12-01:
Know this seems extravagant, but I find I'm most creative at night and really want to use blot on a dark screen.

I'm 100% ok with not having official support for dark mode; but currently the way the turtle is rendered, extensions like "dark reader" will black out the canvas entirely:

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

Short of a full dark-mode, I'd like the ability just to change the color of the pen in the renderer to work with the extension.

AverseABFun, 2024-03-16:
I also want this feature.

Closed 2024-07-13.

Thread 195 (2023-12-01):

Show debugging info in blot

maxwofford, 2023-12-01:
It'd really help for submitting bugs to have a way I can pull these details:

- hash of the script being eval'd (I've had a couple cases where it's unclear if my new script is running b/c it's showing lines I deleted in console.log)
- last run timestamp (for same reason as above)
- current build (ie. how HCB has the git commit hash muted in a footer & detects if it's a dirty build)

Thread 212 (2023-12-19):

Branch protection on the main branch

maxwofford, 2023-12-19:
Currently we don't have branch protection warning users they're merging in a change that breaks the build. I'd like to add branch protection to the `main` branch preventing merge unless CI passes. This wouldn't actually slow down development because  merging into main (currently) just fails silently and leaves production on the previous commit. Branch protection can be overwritten, but requires an extra prompt to ensure the user knows they're merging in something that will fail to deploy.

leomcelroy, 2024-01-05:
Go for it!

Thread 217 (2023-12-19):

Circle (turtle.arc) isn't accurate when less than a whole number of degrees

maxwofford, 2023-12-19:
Context here: https://hackclub.slack.com/archives/C04GCH8A91D/p1702967207674719?thread_ts=1702966457.956549&cid=C04GCH8A91D

Screenshot of some lines that should intersect, but the current arc implementation offsets due to accumulated error:
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

ameya-g-git, 2023-12-21:
hey! coded a recreation of the arc function using some basic mathematics and i've found it works better than the current one. it can handle small, decimal angles nicely!

unsure if i should make a pull request, so ill just put the code i used + a sample screenshot below in markdown

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

```js
const WIDTH = 125;
const HEIGHT = 125;

function pointCoord(angle, radius) { // returns the coords of a point provided a radius and an angle to subtend around a circle of that radius
  return [
    (Math.cos(angle) * radius) - radius,
    Math.sin(angle) * radius
  ]
};

function arc(angle, radius, points) { // yeahhhhh the main function
  const arc = createTurtle();
  const angleRad = angle * (Math.PI / 180); // i like degrees more don't harsh it

  let arcAngle = 0;

  for (let i = 1; i <= points; i++) { // draws the arc by just going to each point on the circle
    arcAngle += angleRad / points;
    arc.goTo(pointCoord(arcAngle, radius));
  };

  arc.translate( // makes it so that the arc doesn't move around while its size changes
    [WIDTH / 2, HEIGHT / 2],
    [-radius, 0]
  );

  return arc
};

const arc1 = arc(1.7, 47, 74); // example, feel free to plug in whatever values you want !

drawTurtles([arc1]); // draw it
```

maxwofford, 2023-12-28:
Great work @ameya-g-git! You should totally contribute this in a PR.

I saw some slight differences between the previous arc function and this implementation.

- it takes in a "points" value. It should ideally just figure out how many steps to iterate with.
- it doesn't factor in the current turtle position and rotation.

Want to take another pass on this? It'd be awesome if you patch this up.

ameya-g-git, 2023-12-29:
thanks for the feedback! here's my thoughts

* the points value was there to give users the ability to resample based on how many points they want, i might just create some sort of function to determine the default value for the points param then
* wdym by factor in the current turtle position and rotation? i was thinking that if the user wanted to transform the arc, they could do so with blot's existing transformation functions, and simply join the turtle once the transformations were complete. should i include parameters to adjust these values?
* as for the off-by-one, im not observing this? the right-most point stays stable no matter how i change the parameters, could you elaborate more?

also, since this isnt exactly art, where would i include my file in the PR? thanks again!

leomcelroy, 2024-01-05:
Want to try it now Max? I updated the arc implementation to work more like this.

Closed 2024-01-14.

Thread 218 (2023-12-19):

Add docs for Blot pcbs

Hugoyhu, 2023-12-19:
- add macro shots of PD board, controller
- add documentation for carrier (make pinout / assembly image)
- add charts for modifying CYPD3177 breakout

shyakachaste, 2024-02-03:
Hey, @Hugoyhu may you please give me more information about that issue, thanks

V205Arduino, 2024-02-03:
@shyakachaste this is probably something that requires you to have the PD dev board and controller.

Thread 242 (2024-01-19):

Assembly instructions page isn't mobile friendly

maxwofford, 2024-01-19:
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

leomcelroy, 2024-02-01:
Just made it link to github page instead.

maxwofford, 2024-02-02:
This was closed by https://github.com/hackclub/blot/commit/544cd861c9d368f133857881e87de1fb335ae1b7

maxwofford, 2024-02-02:
Swapping this to 'wont fix' to clarify we didn't write any changes to the page.

Closed 2024-02-01.

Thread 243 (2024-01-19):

Tool Head pen-holding screw isn't in the instructions & was packed with an incorrect screw

maxwofford, 2024-01-19:
I just went through and built a blot from one of the demo kits in the office.

The tool head has a whole for a screw to hold the pen, but the screw left over from the build looks too long to use and with the wrong size for the allen keys packed in the kit.

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

Additionally there isn't a step at the time of writing to add the screw in https://blot.hackclub.dev/assembly, despite having an instruction to put the nut in the trap for the screw:
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

leomcelroy, 2024-01-27:
This screw is actually supposed to be tightened by hand. That screw could be better though, shorter and with knurling perhaps.

maxwofford, 2024-01-29:
@leomcelroy the screw I found in the kit was too hard to first-time tighten by hand due to https://github.com/hackclub/blot/issues/248 on the tool head. This should either be pre-threaded by screwing it in at the office, or a tool for tightening be provided.

leomcelroy, 2024-03-25:
This is addressed in the new bom.

https://github.com/hackclub/blot/blob/main/docs/BOM.toml

Closed 2024-03-25.

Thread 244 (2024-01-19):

Instructions out of order

maxwofford, 2024-01-19:
I just went through and built a blot from one of the demo kits in the office.

There's an instruction to add a nut to a nut trap in the Printed Rail component:
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

The nut isn't referenced again until Final Assembly, 2 chapters later:
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

In between the steps, the nut fell out of the trap multiple times:
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

I'd suggest adding the nut trap, and adding the belt bearing assembly in the Printed Rail component chapter, then only needing to add the belt during final assembly.

leomcelroy, 2024-02-01:
I agree with reordering this.

leomcelroy, 2024-07-11:
Corrected on new assembly guide.

Closed 2024-07-11.

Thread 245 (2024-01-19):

Using smaller screws on the toolhead v-wheels

maxwofford, 2024-01-19:
I just went through and built a blot from one of the demo kits in the office.

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

The instructions use an m5x35 screw for the toolhead, but they stick out of the toolhead by quite a bit. I was wondering if should swap that with an m5x20 or smaller?

leomcelroy, 2024-01-27:
We wanted to reduce the part count. Open to adding a screw to make it fit better though. Think we actually had decided on doing so in the past.

Closed 2024-07-11.

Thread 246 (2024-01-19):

Stepper motors at office are too tall

maxwofford, 2024-01-19:
I just went through and built a blot from one of the demo kits in the office.

The stepper motors we have are too tall for the blot's legs and the machine rests on it's motors
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

leomcelroy, 2024-02-01:
These are just the wrong motors. Will fix in future by getting the right ones.

Closed 2024-02-01.

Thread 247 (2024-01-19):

Stepper motors lack headers

maxwofford, 2024-01-19:
I just went through and built a blot from one of the demo kits in the office.

The stepper motors are 4-cable steppers that terminate in a split-end wire thread. The board's pinout for the stepper motor drivers is a 4 pin male header. I didn't get a soldering iron in the assembly kit, and without my own soldering kit I won't be able to wire up the stepper motors

leomcelroy, 2024-01-27:
Definitely we don't have the right motors at the office. I'll lock this down and find a sustainable source.

Closed 2024-03-25.

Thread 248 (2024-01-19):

Toolhead nut trap tolerances too tight

maxwofford, 2024-01-19:
I just went through and built a blot from one of the demo kits in the office.

While I assembled it I found the nut traps on the toolhead too tight for the nuts until I drilled them out by screwing through them to sink the nut.

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

This is totally fine by itself, but the instructions asked me to sink nut traps on opposite sides of the part, which meant that gravity wouldn't let the nuts stay in their area. I'd prefer to assemble the bearing assemblies first, then sink the nut second, then flip the part over 3rd so I can do the other side.

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

BrightTheBackpack, 2024-02-05:
Same issue happened here, I just screwed it jn with the nut outside of the nut trap

leomcelroy, 2024-03-25:
This should change with our new part suppliers. Will re-evaluate when we receive test kits.

Closed 2024-03-25.

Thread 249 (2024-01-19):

Document how to re-align V-wheel

maxwofford, 2024-01-19:
 I just went through and built a blot from one of the demo kits in the office.

One of the part boxes contained a v-wheel with a dislocated washer through the middle:
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

This ended up being an easy fix to grab another v-wheel, but I want to flag this issue in case we want more of a process around q/a for shipping parts.

leomcelroy, 2024-01-27:
This isn't broken. You just need to recenter the washer. I take an allen and swirl it around the hole.

maxwofford, 2024-01-29:
Marking this as won't fix then, as it sounds like the underlying issue isn't as big as originally thought.

BrightTheBackpack, 2024-02-17:
Should i add this to tuning.md or assesmbly.,md?

maxwofford, 2024-02-18:
Assembly guide @BrightTheBackpack, because we encounter it while assembling!

Closed 2024-02-20.

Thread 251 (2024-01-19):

How do I flash the blot firmware

maxwofford, 2024-01-19:
I just got through the guide on https://blot.hackclub.dev/assembly and plugged my blot into my computer but it doesn't follow the controls on the editor. I'm assuming I need to flash it with something, but there aren't any instructions to in the guide

BrightTheBackpack, 2024-02-17:
https://github.com/hackclub/blot/blob/main/hardware/motor-control-board/SETUP.md
I'm assuming it's not in assembly because it's supposed to be flashed before it's shipped(I'm assuming you've already found this, close the issue?)

maxwofford, 2024-02-18:
Yep! Closing this now because it's documented in the packing guide

Closed 2024-02-18.

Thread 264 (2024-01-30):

Assembly instruction has wrong number of v-wheels

maxwofford, 2024-01-30:
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

leomcelroy, 2024-02-01:
Fixed with updated BOM.

Closed 2024-02-01.

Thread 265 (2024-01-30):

No position function outwards facing

evan-gan, 2024-01-30:
Could we add an outwards facing position function to blot? Currently there is nothing that does this to my knowledge, and the position is already stored in the class. This should only take a few lines of code.
I believe the function below could be added to [`virtual-gallery/drawing-functions/Turtle.js`](https://github.com/hackclub/blot/blob/main/virtual-gallery/drawing-functions/Turtle.js) to implement this functionality.
```javascript
pos() {
    return this.location
  }
```

BrightTheBackpack, 2024-01-31:
I believe it should be added to astro/src/lib/drawingToolkit
/turtle.ts, not the virtual gallery one

maxwofford, 2024-01-31:
This is a great idea though! I was hoping to have it a couple of times while working on my art.

BrightTheBackpack, 2024-02-04:
also i think t.end sort of does this?

maxwofford, 2024-02-04:
@BrightTheBackpack that's a little confusing. Should this be an alias of that function or does it do something else?

evan-gan, 2024-02-04:
If it a method returned `this.location` from the turtles internals that should be better, because it would work if the turtle had not path. (I believe t.end only works when a path has been made)

Closed 2024-02-22.

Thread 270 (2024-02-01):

Make blot logo in tab black

leomcelroy, 2024-02-01:
It's not visible right now when the tab is selected.

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

shyakachaste, 2024-02-03:
Hello @leomcelroy , iam chaste , iam also the member of hack club , may you please give me more information about that issue, thanks

shyakachaste, 2024-02-03:
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
i have changed that shortcut icom, iam waiting hack club to merge the pull request

Closed 2024-02-05.

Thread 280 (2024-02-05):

Create operation/tuning guide.

leomcelroy, 2024-02-05:
People have struggled with

- belt tensioning
- wiring
- homing of device
- tightening gears on stepper motors

maxwofford, 2024-02-14:
Added a first pass in https://github.com/hackclub/blot/commit/fed2011951b396e2e88be66a9d34539e04bd683e

Closed 2024-03-25.

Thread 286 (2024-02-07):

Add start up music to blot

leomcelroy, 2024-02-07:
Could happen when the blot is powered?
Could happen when data connection is made?

Also indicates if it has Blot firmware.

BrightTheBackpack, 2024-02-16:
Music as in the motor? or the computer?

leomcelroy, 2024-02-25:
Music on the machine. So the motors.

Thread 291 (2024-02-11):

Feature request: Play animation of my turtle drawing my art

zachlatta, 2024-02-11:
I'm in a Blot workshop now and trying to learn the API. I'm finding it a little challenging to get my head around the API.

I wish I could click a button to see a slowed down version of the turtle drawing my code, including the turtle's current orientation as it draws.

V205Arduino, 2024-02-11:
I believe there is/was a issue about this, let me try and dig it up

V205Arduino, 2024-02-11:
#142
(currently kind of stalled, but since you are the amazing founder of hackclub there will be more incentive for this)

BrightTheBackpack, 2024-02-17:
i attempted this last year, i guess i'll give it another shot

BrightTheBackpack, 2024-02-20:
related threads: [estimated time](https://hackclub.slack.com/archives/C04GCH8A91D/p1708428179566799), [animation](https://hackclub.slack.com/archives/C04GCH8A91D/p1708235539369409)

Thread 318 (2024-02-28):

3d printed parts broken in shipping

maxwofford, 2024-02-28:
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

leomcelroy, 2024-03-25:
This should change with our new part suppliers. Will re-evaluate when we receive test kits.

Closed 2024-03-25.

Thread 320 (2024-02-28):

Packing error: servo missing

maxwofford, 2024-02-28:
We got a report from the recipient of blot number 7 that the servo was missing. This shouldn't happen now that there's a packing.md instruction file, but it did. This ticket is to track a root-cause on how it happened.

Closed 2024-03-25.

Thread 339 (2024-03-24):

Missing Links on the Landing Page

ansh3108, 2024-03-24:
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

The "Learn from our guides", "Submission rules" and "Build your own machine". Doesn't seems to redirect anywhere.

leomcelroy, 2024-03-25:
Thanks! Just added them.

Closed 2024-03-25.

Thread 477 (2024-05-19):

Missing, which one should 3D print and which one machine milled(Metal).

salmanfarisvp, 2024-05-19:
Hi, Do we have a document about which part is 3D printed and which part is machined?

leomcelroy, 2024-05-21:
Thanks for inquiring this could be better documented. It's all described in the BOM.toml

https://github.com/hackclub/blot/blob/main/docs/BOM.toml

leomcelroy, 2024-05-21:
The only metal part is the plate on the carriage. It could also be printed in theory but better to be metal if possible.

Closed 2024-07-11.

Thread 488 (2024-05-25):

COBS implementation seems buggy

jackson-smith-a, 2024-05-25:
I don't currently have the hardware to test this so I'm hesitant to make a PR, but I think there's a bug in the firmware's `cobs_encode` and `cobs_decode` implementations. Both issues arise from using the parameter `len`, which is the length of the input buffer, to make sure that they aren't at the end of the output buffer.

In `cobs_encode` this is "fixed" by adding an offset to the length ([here](https://github.com/hackclub/blot/blob/a99d1a9027b034717fe11f75dae72216bc067ad4/hardware/motor-control-board/firmware/firmware.ino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).) However, COBS encoding does not have a one to one relationship between input buffer size and output buffer size; `len + 2` is only the correct size if there is exactly one zero in the input buffer. I think the best course of action is to remove the check entirely and always write the trailing zero, I don't actually see how a situation where we don't want to write it arises -- but I feel like I might be missing something there.

In `cobs_decode` the intention seems to be to [avoid writing the trailing zero](https://github.com/hackclub/blot/blob/a99d1a9027b034717fe11f75dae72216bc067ad4/hardware/motor-control-board/firmware/firmware.ino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) to the output buffer, but again the relationship between `dst_i` and `len` isn't actually consistent; it varies with how many zeros are in the data, so this will sometimes write past the end of the array. I think the correct check would be `i < len` instead of `dst_i < len`, the same as in the `for` loop above.

leomcelroy, 2024-07-11:
Thanks for this thoughtful issue. I just caught this but may not have time to fix it before passing over maintenance of the project to someone else at Hack Club this Friday. I'll keep an eye out if it causes some issues.

maxwofford, 2024-07-12:
@jackson-smith-a if you write up a PR with a little test script, I'm getting my irl blot soon & am happy to test things on it!

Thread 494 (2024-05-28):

Missing Timing Belt details on BOM

salmanfarisvp, 2024-05-28:
Hi, I see the timing belt details are missing in the BOM. Is it possible to share the timing belt details? Is that GT2 Timing belt and pulleys

BrightTheBackpack, 2024-06-30:
It's already in the BOM. it seems like this one: https://openbuildspartstore.com/gt2-2m-timing-belt-by-the-foot/
you can find it by going to the BOM, and ctrl+f timing belt

leomcelroy, 2024-07-11:
It is yes! I think this is corrected in the new BOM.

Closed 2024-07-11.

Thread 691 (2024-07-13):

GH Action: PRs for new art should automatically link "Preview in editor"

maxwofford, 2024-07-13:
automatically posts a “preview in editor” link on each PR which updates when files are changed (ie. like in this PR https://github.com/hackclub/blot/pull/657) should have a link to `https://blot.hackclub.com/editor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`

Aryankpoor, 2024-07-13:
**Hello, I saw help was needed for this issue in slack and I asked if I could work on it .**
Before I work on the solution, I wanted to ask , do you want the link to lead to the added file in the PR or the link that they provided for the code?

maxwofford, 2024-07-13:
@Aryankpoor I want to preview their art. Currently, I need to copy the code from their index.js file, go to https://blot.hackclub.com/editor, then paste that in. Instead I want a link to show up that says "Try this art out in the editor" in the PR and I can click that to get their code prefilled

Aryankpoor, 2024-07-13:
A simple solution would be by pressing . (dot button) which would open up codespaces. Which would open a vscode environment in the browser where you can simply click run and it will run the code

Aryankpoor, 2024-07-13:
No need to add github actions at all

maxwofford, 2024-07-13:
That's not what I'm looking for! Have you tried clicking the links in https://github.com/hackclub/blot/issues/691#issue-2406990193 to see what I mean?

Aryankpoor, 2024-07-13:
I have provided the solution on slack please check

Closed 2024-07-19.

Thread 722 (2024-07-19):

New preview github action shows error

Aryankpoor, 2024-07-19:
The new preview github action for pull requests shows error. A sample of this error can be observed by visiting the preview your blot link in #721 . The error has also been shown in the image below
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

BrightTheBackpack, 2024-07-19:
this happened cause there was a space in the directory, which isn't allowed per 2.2 of the submission rules https://github.com/hackclub/blot/blob/main/docs/GET_A_BLOT.md

Aryankpoor, 2024-07-19:
Closing this as solved.

Closed 2024-07-19.

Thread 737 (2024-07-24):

Blot draws programs from blot JS programs backwards but SVG imports are correctly mirrored

whatwareweb, 2024-07-24:
When printing any program on the Blot from a JS program in the editor, it comes out reversed like shown in the pictures:

web preview:
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

actual blot printout:
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

If you look at the bottom of the pictures you can see the little R symbol there has been reversed.

This issue can be fixed by reversing which wires are plugged into which stepper motor on the real blot. However, when you import an SVG to print, then the SVG is imported backwards. I cannot tell why this was done or whether this was to compensate for this issue or not, but this behavior makes it necessary to keep swapping the stepper motor wires.

The solutions for this issue include

- adding in the blot instructions to swap the stepper motor wires, and do not mirror the image when an SVG is imported
- compensate for the mirroring of the printing in software, such as the JS that sends the commands to the Blot, then do not mirror the SVG import
- Mirror everything in the preview so that users will have an accurate representation of the printout (will break some existing programs)

BrightTheBackpack, 2024-07-24:
we already have instructions on swapping the stepper motor wires in our assembly doc

> The machine will work with any configuration of how the stepper motor pins are plugged in. Depending on how your stepper motors are plugged in the drawing may be mirrored. You can correct this by changing whether the motors are plugged in with the metal pins showing face up or hidden face down. The correct orientation may be some combination of the two. I'll note this again when we cover setting the machine origin.

BrightTheBackpack, 2024-07-24:
I believe svgs are a separate problem, due to the fact that an svg's normal coordinate system goes from top to down, but our coordinate system goes from bottom up

whatwareweb, 2024-07-24:
OK i will look into it then. i will probably PR soon

Closed 2024-07-24.

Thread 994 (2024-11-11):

Fix blot documentation

TuinboonDev, 2024-11-11:
Some functions like: translate, rotate and scale dont work in the online editor. There are some inconsistencies aswell, `new bt.Turtle()` is the correct way to create a turtle but in the [TOOLKIT ](https://github.com/hackclub/blot/blob/main/docs/TOOLKIT-v0.1.0.md) it says `const t = createTurtle()`

BrightTheBackpack, 2024-11-11:
That's the toolkit from version 0.1.0. The current documeIntation can be found in [DOCUMENTATION.MD](https://github.com/hackclub/blot/blob/main/docs/DOCUMENTATION.md)MD. AFAIK the website uses the new docs.

Closed 2024-12-08.

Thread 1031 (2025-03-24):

BOM link broken in assembly guide

leomcelroy, 2025-03-24:
This link

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

 in the assembly guide:

https://github.com/hackclub/blot/blob/main/docs/assembly/ASSEMBLY.md

is broken and should point at:

https://github.com/hackclub/blot/blob/main/docs/BOM.toml

qcoral, 2025-03-31:
Just fixed this, thanks for flagging

Glad to see you still check up on HC :)

Closed 2025-03-31.

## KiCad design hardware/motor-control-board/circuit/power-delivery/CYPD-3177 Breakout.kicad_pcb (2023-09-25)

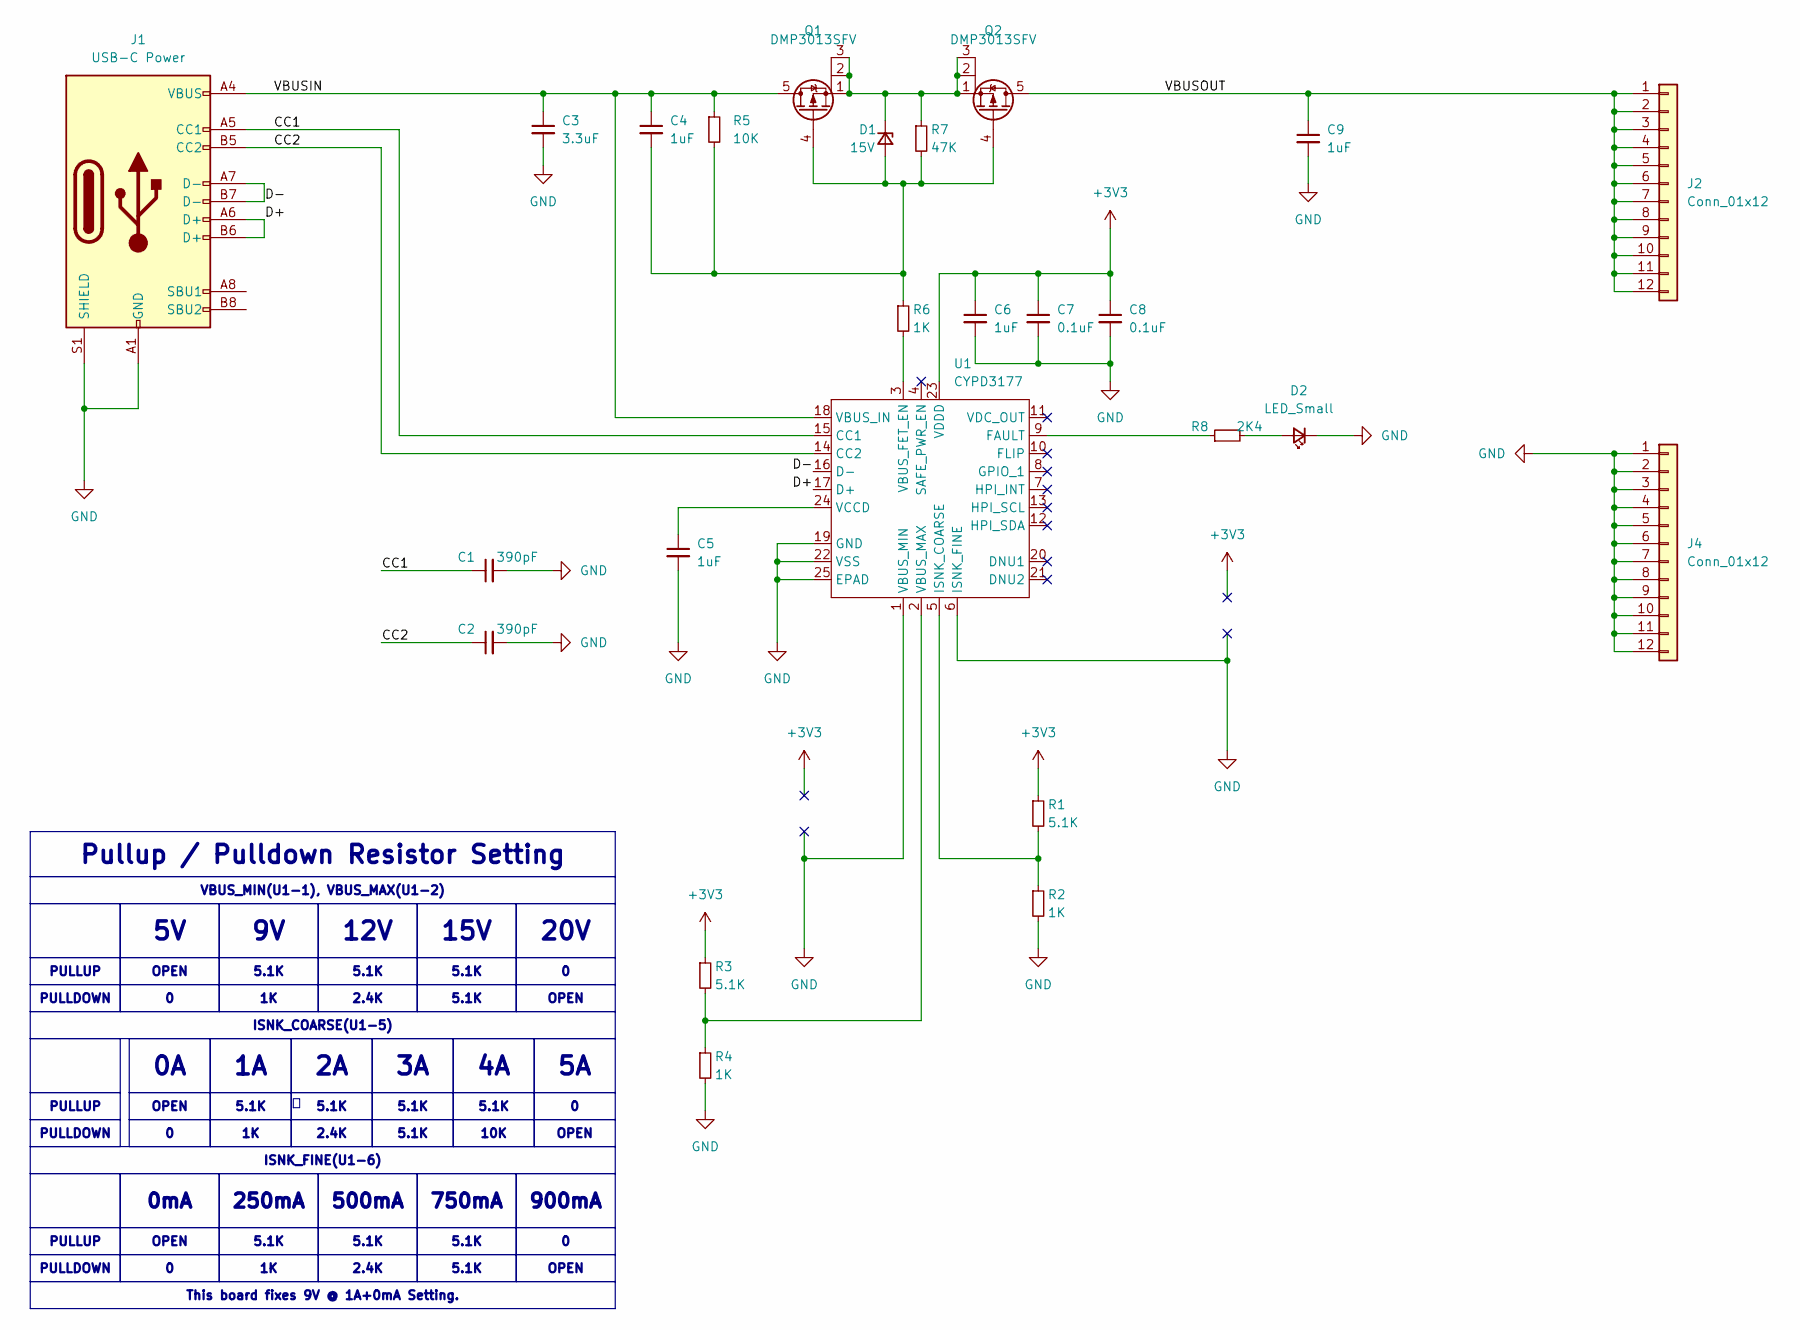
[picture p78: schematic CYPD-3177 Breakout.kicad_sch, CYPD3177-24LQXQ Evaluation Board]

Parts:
C1, C2: 390pF; C_0603_1608Metric_Pad1.08x0.95mm_HandSolder
C3: 3.3uF; C_0805_2012Metric_Pad1.18x1.45mm_HandSolder
C4, C5, C6, C9: 1uF; C_0603_1608Metric_Pad1.08x0.95mm_HandSolder
C7, C8: 0.1uF; C_0603_1608Metric_Pad1.08x0.95mm_HandSolder
D1: 15V; D_SOD-323F
D2: LED_Small; LED_0805_2012Metric_Pad1.15x1.40mm_HandSolder
J1: USB-C Power; USB_C_Receptacle_HRO_TYPE-C-31-M-12
J2, J4: Conn_01x12; PinHeader_1x12_P2.54mm_Vertical
Q1, Q2: DMP3013SFV; Diodes_PowerDI3333-8
R1, R3: 5.1K; R_0603_1608Metric_Pad0.98x0.95mm_HandSolder
R2, R4, R6: 1K; R_0603_1608Metric_Pad0.98x0.95mm_HandSolder
R5: 10K; R_0603_1608Metric_Pad0.98x0.95mm_HandSolder
R7: 47K; R_0603_1608Metric_Pad0.98x0.95mm_HandSolder
R8: 2K4; R_0603_1608Metric_Pad0.98x0.95mm_HandSolder
U1: CYPD3177; QFN-24-1EP_4x4mm_P0.5mm_EP2.7x2.7mm

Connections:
+3V3: C6.1, C7.1, C8.1, R1.1, R3.1, U1.23 (VDDD)
/CC1: C1.1, J1.A5 (CC1), U1.15 (CC1)
/CC2: C2.1, J1.B5 (CC2), U1.14 (CC2)
/D+: J1.A6 (D+), J1.B6 (D+), U1.17 (D+)
/D-: J1.A7 (D-), J1.B7 (D-), U1.16 (D-)
/VBUSIN: C3.1, C4.1, J1.A4 (VBUS), J1.A9 (VBUS), J1.B4 (VBUS), J1.B9 (VBUS), Q1.5 (D), R5.1, U1.18 (VBUS_IN)
/VBUSOUT: C9.1, J2.1, J2.2, J2.3, J2.4, J2.5, J2.6, J2.7, J2.8, J2.9, J2.10, J2.11, J2.12, Q2.5 (D)
GND: C1.2, C2.2, C3.2, C5.2, C6.2, C7.2, C8.2, C9.2, D2.1 (K), J1.A1 (GND), J1.A12 (GND), J1.B1 (GND), J1.B12 (GND), J1.S1 (SHIELD), J4.1, J4.2, J4.3, J4.4, J4.5, J4.6, J4.7, J4.8, J4.9, J4.10, J4.11, J4.12, R2.2, R4.2, U1.1 (VBUS_MIN), U1.6 (ISNK_FINE), U1.19 (GND), U1.22 (VSS), U1.25 (EPAD)
unnamed: C4.2, D1.2 (A), Q1.4 (G), Q2.4 (G), R5.2, R6.1, R7.2
unnamed: D1.1 (K), Q1.1 (S), Q1.2 (S), Q1.3, Q2.1 (S), Q2.2, Q2.3 (S), R7.1
unnamed: D2.2 (A), R8.2
unnamed: R8.1, U1.9 (FAULT)
unnamed: R1.2, R2.1, U1.5 (ISNK_COARSE)
unnamed: R6.2, U1.3 (VBUS_FET_EN)
unnamed: R3.2, R4.1, U1.2 (VBUS_MAX)
unnamed: C5.1, U1.24 (VCCD)

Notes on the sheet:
20V
5.1K
ISNK_COARSE(U1-5)
2.4K
0mA
VBUS_MIN(U1-1), VBUS_MAX(U1-2)
500mA
OPEN
OPEN
10K
15V
This board fixes 9V @ 1A+0mA Setting.
PULLDOWN
12V
250mA
PULLUP
900mA
Pullup / Pulldown Resistor Setting
750mA
ISNK_FINE(U1-6)

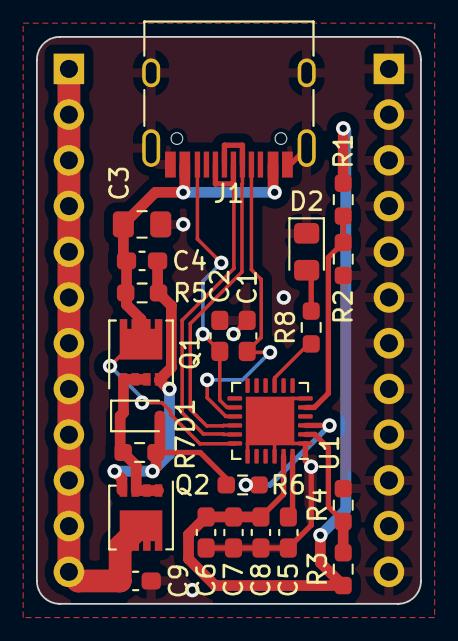
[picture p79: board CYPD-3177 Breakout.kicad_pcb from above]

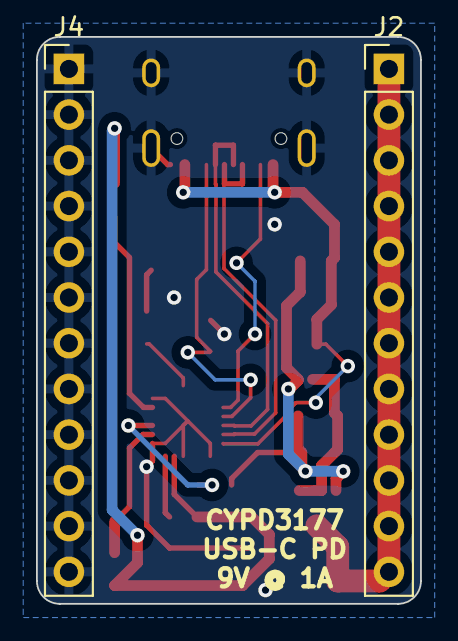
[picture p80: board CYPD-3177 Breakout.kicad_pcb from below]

Board: 2 copper layers, 21.3 x 31.5 mm, 25 parts (2 on the bottom side), 16 nets.

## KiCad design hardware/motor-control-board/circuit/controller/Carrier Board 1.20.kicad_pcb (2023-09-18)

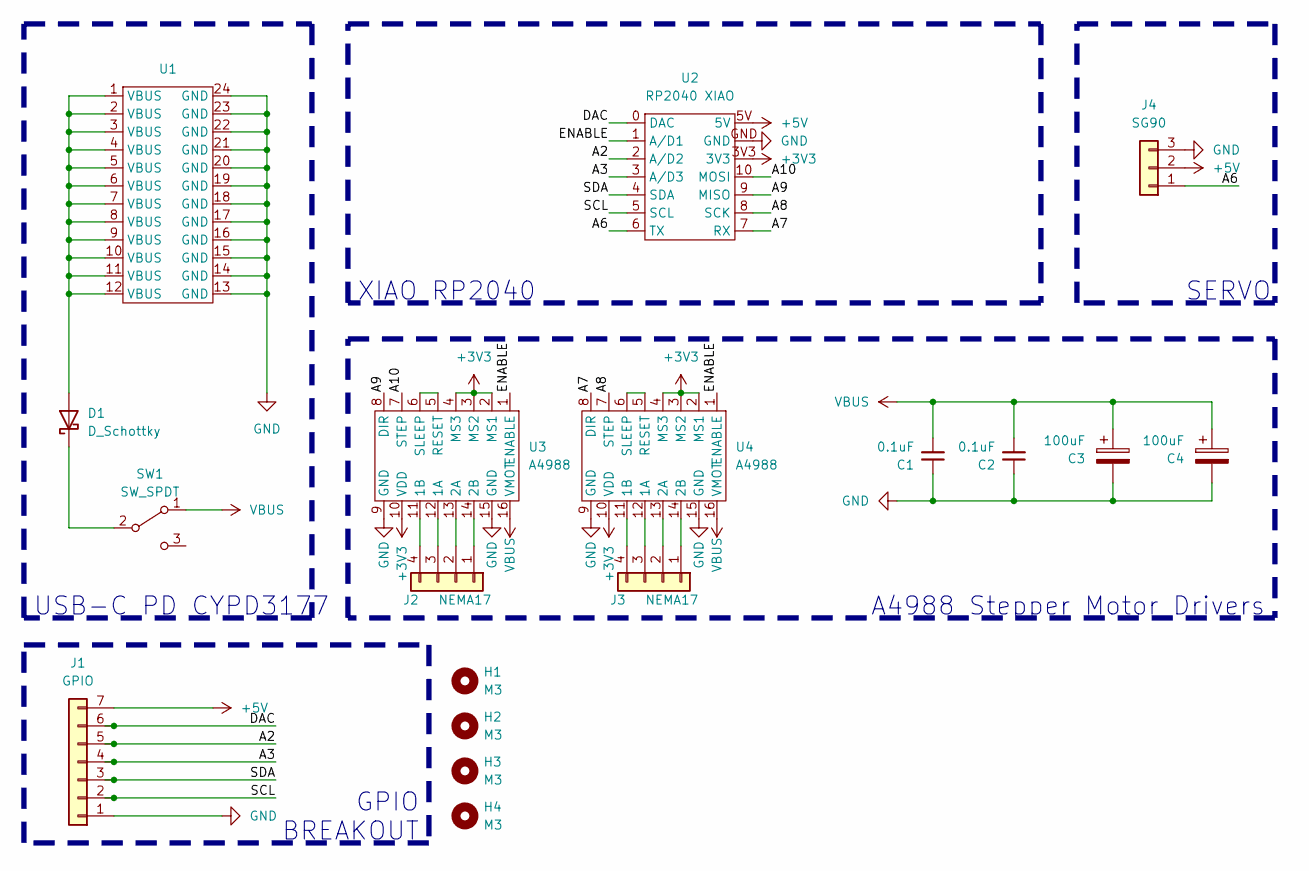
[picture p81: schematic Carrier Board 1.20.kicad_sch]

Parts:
C1, C2: 0.1uF; C_0805_2012Metric_Pad1.18x1.45mm_HandSolder
C3, C4: 100uF; CP_Radial_D6.3mm_P2.50mm
D1: D_Schottky; D_1206_3216Metric_Pad1.42x1.75mm_HandSolder
H1, H2, H3, H4: M3; MountingHole_3.2mm_M3
J1: GPIO; PinSocket_1x07_P2.54mm_Vertical
J2, J3: NEMA17; PinHeader_1x04_P2.54mm_Vertical
J4: SG90; PinHeader_1x03_P2.54mm_Vertical
SW1: SW_SPDT; SWITCH_011CQN
U1: USB-C PD
U2: RP2040 XIAO; QTPYXIAORP2040
U3, U4: A4988

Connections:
+3V3: U2.3V3, U3.2 (MS1), U3.3 (MS2), U3.4 (MS3), U3.10 (VDD), U4.2 (MS1), U4.3 (MS2), U4.4 (MS3), U4.10 (VDD)
+5V: J1.7, J4.2, U2.5V
/A2: J1.5, U2.2 (A/D2)
/A3: J1.4, U2.3 (A/D3)
/A6: J4.1, U2.6 (TX)
/A7: U2.7 (RX), U4.8 (DIR)
/A8: U2.8 (SCK), U4.7 (STEP)
/A9: U2.9 (MISO), U3.8 (DIR)
/A10: U2.10 (MOSI), U3.7 (STEP)
/DAC: J1.6, U2.0 (DAC)
/ENABLE: U2.1 (A/D1), U3.1 (ENABLE), U4.1 (ENABLE)
/SCL: J1.2, U2.5 (SCL)
/SDA: J1.3, U2.4 (SDA)
GND: C1.1, C2.1, C3.2, C4.2, J1.1, J4.3, U1.13 (GND), U1.14 (GND), U1.15 (GND), U1.16 (GND), U1.17 (GND), U1.18 (GND), U1.19 (GND), U1.20 (GND), U1.21 (GND), U1.22 (GND), U1.23 (GND), U1.24 (GND), U2.GND, U3.9 (GND), U3.15 (GND), U4.9 (GND), U4.15 (GND)
unnamed: D1.2 (A), U1.1 (VBUS), U1.2 (VBUS), U1.3 (VBUS), U1.4 (VBUS), U1.5 (VBUS), U1.6 (VBUS), U1.7 (VBUS), U1.8 (VBUS), U1.9 (VBUS), U1.10 (VBUS), U1.11 (VBUS), U1.12 (VBUS)
unnamed: D1.1 (K), SW1.2 (B)
unnamed: J2.1, U3.14 (2B)
unnamed: J2.2, U3.13 (2A)
unnamed: J2.3, U3.12 (1A)
unnamed: J2.4, U3.11 (1B)
unnamed: J3.1, U4.14 (2B)
unnamed: J3.2, U4.13 (2A)
unnamed: J3.3, U4.12 (1A)
unnamed: J3.4, U4.11 (1B)
unnamed: U3.5 (RESET), U3.6 (SLEEP)
unnamed: U4.5 (RESET), U4.6 (SLEEP)
VBUS: C1.2, C2.2, C3.1, C4.1, SW1.1 (A), U3.16 (VMOT), U4.16 (VMOT)

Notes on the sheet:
USB-C PD CYPD3177
SERVO
A4988 Stepper Motor Drivers
XIAO RP2040
GPIO BREAKOUT

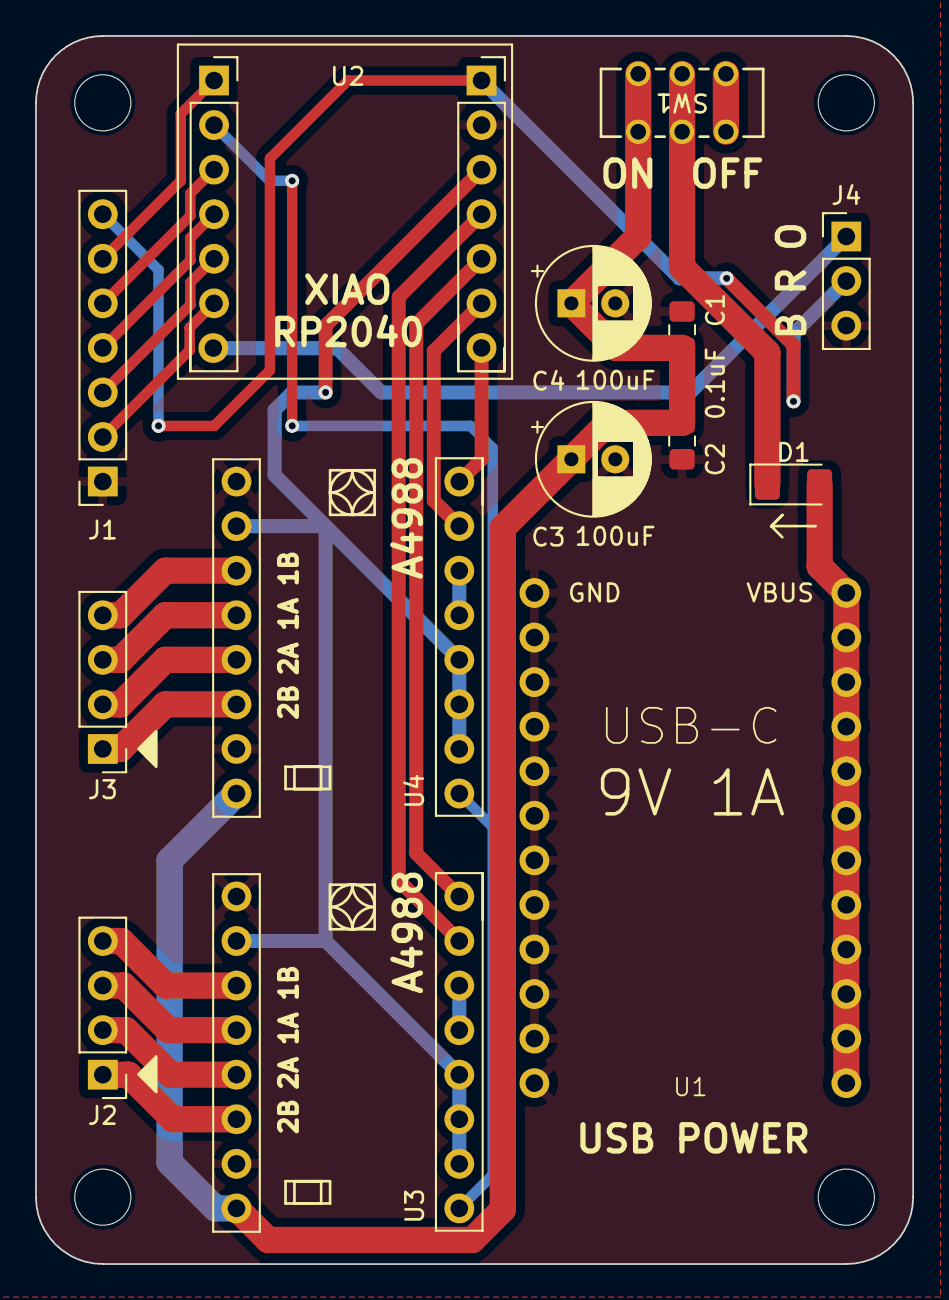
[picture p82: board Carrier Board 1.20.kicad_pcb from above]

Board: 2 copper layers, 50.0 x 70.0 mm, 18 parts (0 on the bottom side), 27 nets.

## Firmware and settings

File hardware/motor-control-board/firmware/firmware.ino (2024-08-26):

#include <Servo.h>

#define SPU 80 // 20 teeth pulley, 16 microstep, 2mm a tooth belt, 16*200 microsteps per turn  == (16*200)/(20*2) == 80
#define PIN_SERVO D6

Servo servo;

typedef uint8_t (*CallbackFunction)(uint8_t*, int, uint8_t*);

struct EventCallback {
  String event;
  CallbackFunction callback;
};


float pos[] = {0, 0};

const int motor1StepPin = D10;
const int motor1DirPin = D9;
const int motor2StepPin = D8;
const int motor2DirPin = D7;

const int enablePin = D1;

void setup() {  
  servo.attach(PIN_SERVO);

  Serial.begin(9600);

  // on("light", onLight);
  on("go", go);
  on("servo", moveServo);
  on("motorsOn", motorsOn);
  on("motorsOff", motorsOff);
  on("moveTowardsOrigin", moveTowardsOrigin);
  on("setOrigin", setOrigin);

  pinMode(motor1StepPin, OUTPUT);
  pinMode(motor1DirPin, OUTPUT);
  pinMode(motor2StepPin, OUTPUT);
  pinMode(motor2DirPin, OUTPUT);

  pinMode(enablePin, OUTPUT); // enable pin

  pinMode(PIN_LED, OUTPUT);

  startupIndicator(); // once startup is finished, indicate to user
}

void loop() {
  readSerial();
}

void startupIndicator() {
  // flash LED to indicate board is initialized
  for (int i = 0; i < 3; i++) {
    digitalWrite(PIN_LED, 0);
    delay(200);
    digitalWrite(PIN_LED, 1);
    delay(200);
  }
}

uint8_t onLight(uint8_t* payload, int length, uint8_t* reply) {
  uint8_t value = payload[0];

  // Serial.println("light it up");

  digitalWrite(PIN_LED, value);

  return 0;
}

uint8_t motorsOn(uint8_t* payload, int length, uint8_t* reply) {
  digitalWrite(enablePin, 0);
  return 0;
}

uint8_t motorsOff(uint8_t* payload, int length, uint8_t* reply) {
  digitalWrite(enablePin, 1);
  return 0;
}

uint8_t moveTowardsOrigin(uint8_t* payload, int length, uint8_t* reply) {
  float x = pos[0];
  float y = pos[1];

  // this ternary may not be neccesary
  goTo(
    x + ( x < 0 ? 10 : -10), 
    y + ( y < 0 ? 10 : -10)
  );

  return 0;
}

uint8_t setOrigin(uint8_t* payload, int length, uint8_t* reply) {
  pos[0] = 0;
  pos[1] = 0;

  return 0;
}


/* ------------------------------------------------------------ */

int bufferIndex = 0;
uint8_t msgBuffer[100];

void readSerial() {
  while (Serial.available() > 0) {
    uint8_t incoming = Serial.read(); 

    msgBuffer[bufferIndex] = incoming;

    if (incoming != 0) {
      bufferIndex++;
      continue; // Proceed to the next byte if current byte is not null
    }

    // Serial.print("RECEIVED: ");
    // for (int i = 0; i < bufferIndex; i++) {
    //   Serial.print(msgBuffer[i]);
    //   Serial.print(", ");
    // }
    // Serial.println("DONE");

    // Now we have a full message, perform COBS decoding
    uint8_t decoded[bufferIndex];
    cobs_decode(decoded, msgBuffer, bufferIndex);

    // Serial.print("DECODED: ");
    // for (int i = 0; i < bufferIndex; i++) {
    //   Serial.print(decoded[i]);
    //   Serial.print(", ");
    // }
    // Serial.println("DONE");

    // Parse the decoded message
    int i = 0;

    uint8_t msgLength = decoded[i];
    // Serial.print("MSG-LENGTH: ");
    // Serial.println(msgLength);

    uint8_t msgArr[msgLength];
    i++;
    while (i < 1 + msgLength) {
      msgArr[i-1] = decoded[i];
      i++;
    }

    // Serial.print("MSGARR: ");
    // for (int i = 0; i < msgLength; i++) {
    //   Serial.print(msgArr[i]);
    //   Serial.print(", ");
    // }
    // Serial.println("MSGARR-END");

    uint8_t payloadLength = decoded[i];
    uint8_t payload[payloadLength];
    i++;
    while (i < 1 + msgLength + 1 + payloadLength) {
      payload[i-1-msgLength-1] = decoded[i];
      i++;
    }

    uint8_t msgCount = decoded[i];

    // String msg = String((char*)msgArr);
    String msg = byteArrayToString(msgArr, msgLength);

    // Serial.println(msg);

    // printArray("PAYLOAD", payload, payloadLength);

    // Serial.print("MSGCOUNT: ");
    // Serial.println(msgCount);

    bool triggered = triggerEvent(msg, payload, payloadLength, msgCount);

    bufferIndex = 0; // Reset the buffer for the next message
  }
}

/* ------------------------------------------------------------ */



const int MAX_EVENTS = 255; // Maximum number of events to store, adjust as needed
EventCallback eventCallbacks[MAX_EVENTS];
int eventCount = 0;

const int REPLY_PAYLOAD_LENGTH = 255;
uint8_t reply[REPLY_PAYLOAD_LENGTH];

void on(String event, CallbackFunction callback) {
  if (eventCount < MAX_EVENTS) {
    eventCallbacks[eventCount].event = event;
    eventCallbacks[eventCount].callback = callback;
    eventCount = (eventCount + 1) % MAX_EVENTS;
  } else {
    // Serial.println("Max number of events reached. Wrapping events.");
  }
}

bool triggerEvent(String event, uint8_t* payload, int payloadLength, uint8_t msgCount) {
  for (int i = 0; i < eventCount; i++) {
    if (eventCallbacks[i].event == event) {
      // want to pass payload and payloadLength, need to get response payload
      uint8_t reply_length = eventCallbacks[i].callback(payload, payloadLength, reply);

      sendAck(msgCount, reply, reply_length);
      return true;
    }
  }

  // Serial.println(" No event registered.");
  return false;
}

const int arrayLength = 7; // + length;
uint8_t byteArray[arrayLength];

void sendAck(uint8_t msgCount, uint8_t* reply, uint8_t length) {
  // Serial.println("SEND ACK");

  // int arrayLength = 7; // + length;
  // static uint8_t byteArray[arrayLength];

  byteArray[0] = 0x03;
  byteArray[1] = 0x61;
  byteArray[2] = 0x63;
  byteArray[3] = 0x6B;
  byteArray[4] = 0x00;
  byteArray[5] = msgCount;
  byteArray[6] = 0x0A;

  // byteArray[4] = length;
  // for (int i = 0; i < length; i++) {
  //   byteArray[i+5] = reply[i];
  // }
  // byteArray[5+length] = msgCount;
  // byteArray[6+length] = 0x0A;

  // Serial.println(msgCount);
  // printArray("ACK", byteArray, 5+length);

  Serial.write(byteArray, arrayLength);
      
  // uint8_t byteArrayEncoded[arrayLength + 2]; // +2 for possible COBS overhead
  // cobs_encode(byteArrayEncoded, byteArray, arrayLength);
  // Serial.write(byteArrayEncoded, arrayLength + 2);

  // printArray("ENCODED-ACK", byteArray, 5+length);

}

/* ------------------------------------------------------------ */

void cobs_encode(uint8_t *dst, const uint8_t *src, size_t len) {
    size_t read_index = 0;
    size_t write_index = 1;
    size_t code_index = 0;
    uint8_t code = 1;

    while (read_index < len) {
        if (src[read_index] == 0) {
            dst[code_index] = code;
            code = 1;
            code_index = write_index++;
            read_index++;
        } else {
            dst[write_index++] = src[read_index++];
            code++;
            if (code == 0xFF) {
                dst[code_index] = code;
                code = 1;
                code_index = write_index++;
            }
        }
    }

    dst[code_index] = code;

    // Add trailing zero
    if (write_index < len + 2) {
        dst[write_index] = 0;
    }
}

void cobs_decode(uint8_t *dst, const uint8_t *src, size_t len) {
    size_t i, j, dst_i = 0;
    for (i = 0; i < len;) {
        uint8_t code = src[i++];
        for (j = 1; j < code && i < len; j++) {
            dst[dst_i++] = src[i++];
        }
        if (code < 0xFF && dst_i < len) {
            dst[dst_i++] = 0;
        }
    }
}

/* ------------------------------------------------------------ */

// TODO: THINK THIS IS BUGGY
void cobs_print(const String& message) {
  // Convert the message to a byte array
  int length = message.length();
  uint8_t byteArray[length + 1]; // +1 for the null terminator
  message.getBytes(byteArray, length + 1);

  // Prepare the buffer for the encoded message
  uint8_t encoded[length + 2]; // +2 for possible COBS overhead
  
  // Perform COBS encoding
  cobs_encode(encoded, byteArray, length + 1);

  // Send the encoded message
  Serial.write(encoded, length + 2); // Write the encoded bytes
}

/* ------------------------------------------------------------ */

float read_float(uint8_t* buffer, int index) {
  uint8_t byte0 = buffer[index];
  uint8_t byte1 = buffer[index+1];
  uint8_t byte2 = buffer[index+2];
  uint8_t byte3 = buffer[index+3];

  uint8_t byteArray[] = {byte0, byte1, byte2, byte3};
  float floatValue;
  memcpy(&floatValue, &byteArray, sizeof(floatValue));

  return floatValue;
}

int read_int(uint8_t* buffer, int index) {
  uint8_t byte0 = buffer[index];
  uint8_t byte1 = buffer[index+1];
  uint8_t byte2 = buffer[index+2];
  uint8_t byte3 = buffer[index+3];

  uint8_t byteArray[] = {byte0, byte1, byte2, byte3};
  int value;
  memcpy(&value, &byteArray, sizeof(value));

  return value;
}

String byteArrayToString(byte arr[], int length) {
  String result = "";

  for (int i = 0; i < length; i++) {
    result += (char)arr[i]; // Convert each byte to a character and append it to the string
  }

  return result;
}

/* ------------------------------------------------------------------------ */

#define EPSILON 0.01

void goTo(float x, float y) {

  // Serial.println("START GOTO");

  // Set your target distances for each motor (in steps)
  float motor1Target = (x + y) - pos[0];
  float motor2Target = (y - x) - pos[1];

  // Set motor direction based on target values
  digitalWrite(motor1DirPin, motor1Target >= 0 ? HIGH : LOW);
  digitalWrite(motor2DirPin, motor2Target >= 0 ? HIGH : LOW);

  // Calculate the relative speeds and maximum duration for both motors
  float maxSteps = max(abs(motor1Target), abs(motor2Target));
  float motor1Speed = abs(motor1Target) / maxSteps;
  float motor2Speed = abs(motor2Target) / maxSteps;

  unsigned long stepDuration = 500; // The time it takes to perform one step in microseconds
  unsigned long motor1StepInterval = stepDuration / motor1Speed;
  unsigned long motor2StepInterval = stepDuration / motor2Speed;

  // Initialize variables for step timing
  unsigned long motor1PrevStepTime = 0;
  unsigned long motor2PrevStepTime = 0;
  float motor1Step = 0;
  float motor2Step = 0;

  // Loop until both motors reach their target steps
  while (abs(motor1Target - motor1Step) > EPSILON || abs(motor2Target - motor2Step) > EPSILON) {


    unsigned long currentTime = micros();

    // Motor 1
    if (abs(motor1Target - motor1Step) > EPSILON && ((currentTime - motor1PrevStepTime) >= motor1StepInterval)) {
      digitalWrite(motor1StepPin, HIGH);
      delayMicroseconds(1);
      digitalWrite(motor1StepPin, LOW);
      delayMicroseconds(1);

      motor1Step += (motor1Target >= 0 ? 1.0 : -1.0)/SPU;
      motor1PrevStepTime = currentTime;
    }

    // Motor 2
    if (abs(motor2Target - motor2Step) > EPSILON && ((currentTime - motor2PrevStepTime) >= motor2StepInterval)) {
      digitalWrite(motor2StepPin, HIGH);
      delayMicroseconds(1);
      digitalWrite(motor2StepPin, LOW);
      delayMicroseconds(1);

      motor2Step += (motor2Target >= 0 ? 1.0 : -1.0)/SPU;
      motor2PrevStepTime = currentTime;
    }
  }

  // Serial.println("END GOTO");

  pos[0] += motor1Step;
  pos[1] += motor2Step;
}

uint8_t go(uint8_t* payload, int length, uint8_t* reply) {
  float x = read_float(payload, 0);
  float y = read_float(payload, 4);
  
  goTo(x, y);

  return 0;
}

uint8_t moveServo(uint8_t* payload, int length, uint8_t* reply) {
  int angle = read_int(payload, 0);
  
  servo.writeMicroseconds(angle);

  return 0;
}

/* ------ */

void printArray(String label, uint8_t* arr, int arrSize) {
  Serial.print(label);
  Serial.print("-BEGIN: ");
  for (int i = 0; i < arrSize; i++) {
    Serial.print(arr[i]);
    Serial.print(", ");
  }
  Serial.print(label);
  Serial.println("-END");
}

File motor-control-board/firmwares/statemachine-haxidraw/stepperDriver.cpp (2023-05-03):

#include "stepperDriver.h"

// change pins
int pins_dir[N_AXIS] = { D5, D8 };
int pins_step[N_AXIS] = { D6, D7 };

uint32_t pins_dir_bm[N_AXIS];
uint32_t pins_step_bm[N_AXIS];

void stepper_init(void){
  for (int i = 0; i < N_AXIS; i++) {
    pinMode(pins_step[i], OUTPUT);
    pinMode(pins_dir[i], OUTPUT);
    pins_step_bm[i] = (uint32_t)(1 << pins_step[i]);
    pins_dir_bm[i] = (uint32_t)(1 << pins_dir[i]);
  }
}

void stepper_step(int i, boolean dir) {
  if (dir) {
    sio_hw->gpio_set = pins_dir_bm[i];
  } else {
    sio_hw->gpio_clr = pins_dir_bm[i];
  }
  sio_hw->gpio_set = pins_step_bm[i];
  delayMicroseconds(10);
  sio_hw->gpio_clr = pins_step_bm[i];
}

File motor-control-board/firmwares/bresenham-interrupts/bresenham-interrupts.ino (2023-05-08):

#include "pico/stdlib.h"
#include "hardware/timer.h"
#include "hardware/irq.h"

#define SPU 400

float pos[] = {0, 0};

const int motor1StepPin = D6;
const int motor1DirPin = D5;
const int motor2StepPin = D7;
const int motor2DirPin = D8;

const uint32_t interruptFrequency = 20000; // 20,000 Hz, or 50 microseconds interval

const unsigned long stepDuration = 500; // The time it takes to perform one step in microseconds
volatile float motor1Step = 0;
volatile float motor2Step = 0;
volatile float motor1Target = 0;
volatile float motor2Target = 0;
volatile unsigned long motor1StepInterval = 0;
volatile unsigned long motor2StepInterval = 0;
volatile unsigned long motor1PrevStepTime = 0;
volatile unsigned long motor2PrevStepTime = 0;


void setup() {
  pinMode(motor1StepPin, OUTPUT);
  pinMode(motor1DirPin, OUTPUT);
  pinMode(motor2StepPin, OUTPUT);
  pinMode(motor2DirPin, OUTPUT);

  initTimer();
}

void loop() {

  readSerial();
  // Add a delay or other code here if you want to run the movement repeatedly
  // delay(1000);
}

void goTo(float x, float y) {
  // Set your target distances for each motor (in steps)
  motor1Target = (x + y) - pos[0];
  motor2Target = (y - x) - pos[1];

  // Set motor direction based on target values
  digitalWrite(motor1DirPin, motor1Target >= 0 ? HIGH : LOW);
  digitalWrite(motor2DirPin, motor2Target >= 0 ? HIGH : LOW);

  // Calculate the relative speeds and maximum duration for both motors
  float maxSteps = max(abs(motor1Target), abs(motor2Target));
  float motor1Speed = abs(motor1Target) / maxSteps;
  float motor2Speed = abs(motor2Target) / maxSteps;

  motor1StepInterval = stepDuration / motor1Speed;
  motor2StepInterval = stepDuration / motor2Speed;

  // Initialize variables for step timing
  motor1PrevStepTime = micros();
  motor2PrevStepTime = motor1PrevStepTime;

  // Reset step counters
  motor1Step = 0;
  motor2Step = 0;
}

void step_ISR() {
  unsigned long currentTime = micros();

  // Motor 1
  if (abs(motor1Step) < abs(motor1Target) && currentTime - motor1PrevStepTime >= motor1StepInterval) {
    digitalWrite(motor1StepPin, HIGH);
    delayMicroseconds(1);
    digitalWrite(motor1StepPin, LOW);
    delayMicroseconds(1);

    motor1Step += (motor1Target >= 0 ? 1.0 : -1.0) / SPU;
    motor1PrevStepTime = currentTime;
  }

  // Motor 2
  if (abs(motor2Step) < abs(motor2Target) && currentTime - motor2PrevStepTime >= motor2StepInterval) {
    digitalWrite(motor2StepPin, HIGH);
    delayMicroseconds(1);
    digitalWrite(motor2StepPin, LOW);
    delayMicroseconds(1);

    motor2Step += (motor2Target >= 0 ? 1.0 : -1.0) / SPU;
    motor2PrevStepTime = currentTime;
  }

  // Update position when both motors reach their target steps
  if (abs(motor1Step) >= abs(motor1Target) && abs(motor2Step) >= abs(motor2Target)) {
    pos[0] += motor1Step;
    pos[1] += motor2Step;
  }
}

void initTimer() {
  // Select a free timer
  int timerID = 0;
  hardware_alarm_claim(timerID);

  // Set the frequency
  uint32_t ticks = clock_get_hz(clk_sys) / interruptFrequency;
  hardware_timer_set_ticks(timerID, ticks);

  // Enable the interrupt
  hardware_timer_clear_overflow(timerID);
  irq_set_exclusive_handler(TIMER_IRQ_0, step_ISR);
  irq_set_enabled(TIMER_IRQ_0, true);
  hardware_timer_set_repeating(timerID, true);
}


int bufferIndex = 0;
uint8_t msgBuffer[100];

void readSerial() {
  if (Serial.available() > 0) {
    uint8_t incoming = Serial.read(); 
    if (incoming == 0x0A) { // \n terminated
      uint8_t msg = msgBuffer[0];
      if (msg == 0x00) { // "go"

        float x = read_float(msgBuffer, 1);
        float y = read_float(msgBuffer, 5);
        
        goTo(x, y);
      }

      // if (msg == 0x01) { // "accel"
      //   float value = read_float(msgBuffer, 1);
      //   ACCEL = value;
      //   Serial.print("accel: ");
      //   Serial.println(value);
      // }

      // if (msg == 0x02) { // "maxSpeed"
      //   float value = read_float(msgBuffer, 1);
      //   MAX_SPEED = value;
      //   Serial.print("speed: ");
      //   Serial.println(value);
      // }

      if (msg == 0x03) { // "servo"
        int angle = read_int(msgBuffer, 1);
        // servo.write(angle);

        Serial.print("servo: ");
        Serial.println(angle);
      }

      bufferIndex = 0;
    } else {
      msgBuffer[bufferIndex] = incoming;
      bufferIndex = bufferIndex + 1;

      if (bufferIndex >= 100) {
        Serial.println("Communication buffer overflow.");
      }
    }
  }
}

float read_float(uint8_t* buffer, int index) {
  uint8_t byte0 = buffer[index];
  uint8_t byte1 = buffer[index+1];
  uint8_t byte2 = buffer[index+2];
  uint8_t byte3 = buffer[index+3];

  uint8_t byteArray[] = {byte0, byte1, byte2, byte3};
  float floatValue;
  memcpy(&floatValue, &byteArray, sizeof(floatValue));

  return floatValue;
}

int read_int(uint8_t* buffer, int index) {
  uint8_t byte0 = buffer[index];
  uint8_t byte1 = buffer[index+1];
  uint8_t byte2 = buffer[index+2];
  uint8_t byte3 = buffer[index+3];

  uint8_t byteArray[] = {byte0, byte1, byte2, byte3};
  int value;
  memcpy(&value, &byteArray, sizeof(value));

  return value;
}

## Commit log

2024-03-25 wip updated control board
    [Control Board.kicad_pcb, Control Board.kicad_sch]
2024-03-25 update landing page
2024-03-25 add gallery filter
2024-04-04 add call to action button
2024-04-05 fixing landing sizing
2024-04-09 remove wip from blot
    [arm.obj, feet.obj, penholder.obj]
2024-04-09 Update landing.js
    add sign up confirmation
2024-04-16 Added my work, Generative Mountain Art
2024-04-18 Procedural Fingerprint by Jeremy
2024-05-09 update blot parts
    [1x_BeltClip.stl, 1x_Carriage.stl, 1x_CarriagePlate.dxf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]
2024-06-07 my art
    its a 3d wireframe renderer!
2024-06-29 Created index.js
    This code will create a generic 3d Printer image. Heavy inspiration from the Bambu A1 mini and Prusa Mini. I hope to obtain one some day. X and Z axis move. The image on the screen also changes.
2024-07-05 update bom
2024-07-10 update assembly guide
2024-07-10 update assembly links
2024-07-10 remove old assembly guide
2024-07-11 remove kicad file
    [Control Board.kicad_pcb, Control Board.kicad_sch]
2024-07-11 add easyeda control board
2024-07-18 Allow for wide images to be cropped to size
    Previously, wide images would be squashed to fit inside the frame of the document. Now, both long and wide images will be cropped to fit inside the document instead.
2024-07-18 Significantly improve error messages
    This adds assertations to all of the built-in
    functions in Blot to throw meaningful errors when
    the wrong arguments are passed. It also upgrades
    the stack trace parsing logic, using V8's object
    representation and a regex built based on the
    SpiderMonkey and JavaScriptCore source code.
    Safari (JavaScriptCore) does not keep track of
    line numbers within eval'd code, so a hack is used
    to construct a data URL and import it when it is
    detected to be nessesary.
    The previous version of Blot would give unhelpful
    errors like "t is not defined" on line 0, and line
    numbers only ever worked on Chrome in some cases.
    Now, it will give helpful errors explaining what
    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
2024-07-29 General improvements Add copy button, improve terminology, remove unnecessary errors
2024-08-02 Fix a number of bugs in the new error messages
    Fix bugs that were discovered when testing the new error message system
    against every gallery function and open PR. It fixes a number of subtle
    logic bugs, adds a new "numberArray" type for the bt.noise function, and
    improves performance by not checking every element of large arrays.
    This commit is a combination of the following 7 commits:
    Fix bug in noise.js to satisfy assertions
    Make logic for determining the type of an array more accurate and robust
    Add numberArray type for the bt.noise function
    Correctly mark the second argument to bt.simplify as optional
    Make a point count as a numberArray
    Fix handling of special case expected types withi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
2024-08-02 Update ASSEMBLY.md
    its 6 mm, not 5 mm
2024-08-21 Revert "make ready to deploy on vercel"
    [server.js]
2024-08-22 hopefully fixed heroku crash
    [server.js]
2024-08-22 Revert "Revert "make ready to deploy on vercel""
    This reverts commit d3220db7
    [server.js]
2024-09-06 Fix: Accidentally made art 180mm not 125mm
2024-09-25 fix: error in ASSEMBLY.md
2024-10-08 Update index.js
    - Made it a box of cupcakes rather than just 1
    - Cupcake drawing is function-driven, with custom placement and size
    - Color cupcake looks better (doesn't use outline color)
    - Debug tools using text printing (useful in school when I don't have access to console)
    - Use actual collision detection rather than just trying to guess using circles
2024-11-21 Update ASSEMBLY.md
    Made various changes:
    - Some steps I found when I was building the blot were mistyped or missing
    - Added a couple debugging tips so people can learn from my failures
2025-01-06 Removed sticker button
2025-03-31 Update ASSEMBLY.md (fixed broken link to BOM)
2026-04-20 Tighten RMRRF fork note wording
